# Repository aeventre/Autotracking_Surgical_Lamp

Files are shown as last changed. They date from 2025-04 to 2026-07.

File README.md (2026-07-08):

# AutoTracking Surgical Robot lamp



## Table of Contents
- [AutoTracking Surgical Robot lamp](#autotracking-surgical-robot-lamp)
  - [Table of Contents](#table-of-contents)
  - [Overview](#overview)
  - [Background](#background)
  - [Acknowledgments](#acknowledgments)
- [System Overview](#system-overview)
- [Software Design](#software-design)
  - [Setup](#setup)
  - [Package Overview](#package-overview)
    - [`command_manager`](#command_manager)
    - [`lamp_gui`](#lamp_gui)
    - [`remote_tracker`](#remote_tracker)
    - [`camera_calibration`](#camera_calibration)
    - [`goal_pose_executor`](#goal_pose_executor)
    - [`controller_coms`](#controller_coms)
    - [`surg_bot_description`](#surg_bot_description)
    - [`surg_bot_moveit_config`](#surg_bot_moveit_config)
  - [Launch Configurations](#launch-configurations)
- [Electrical Design](#electrical-design)
- [CAD](#cad)
  - [3D Printed Components of Surgical Robot](#3d-printed-components-of-surgical-robot)
  - [Sensors and Servos](#sensors-and-servos)
  - [Bill of materials for Surgical Robot](#bill-of-materials-for-surgical-robot)
  - [Bill of Materials for Surgical Robot Base](#bill-of-materials-for-surgical-robot-base)

## Overview
An open-source ROS 2 and MoveIt 2 surgical lamp capable of autonomous real-time tracking of a handheld remote using monocular vision and 3D pose estimation. 

## Background
This project aims to develop a solution to the challenges posed by modern surgical lamps,
particularly focused on the ceiling-mounted lamps. The proposed solution is a responsive
surgical lamp that uses real-time tracking and automated movement to adjust its lighting
position. This approach minimizes manual interaction, reduces delays and allows support staff
to remain focused on higher priority clinical responsibilities

# System Overview
  

# Software Design

This ROS 2 workspace contains all packages required for the Auto-Tracking Surgical Lamp system. The lamp uses 3D pose tracking of a handheld remote (via green ball detection) to plan and execute motions in real-time, with fallback modes for manual GUI control and demo sequences. The system is built using ROS 2 Jazzy and MoveIt 2.

## Setup

To build and source the workspace:

```bash
cd /path/to/ros2_ws
source /opt/ros/jazzy/setup.bash
rosdep install --from-paths src --ignore-src -r -y
colcon build
source install/setup.bash
```

## Package Overview

software_architecture

### `command_manager`

Manages the system's behavior based on user input. It switches between modes such as idle, manual control, tracking, zeroing, and demo.

**Subscriptions**
- `/system_mode` (`std_msgs/Int32`)
- `/remote_pose` (`geometry_msgs/PoseStamped`)
- `/remote_orientation` (`geometry_msgs/QuaternionStamped`)
- `/user_command` (`surg_lamp_msgs/UserCommand`)

**Publications**
- `/goal_pose` (`geometry_msgs/PoseStamped`)
- `/joint_commands` (`std_msgs/Float64MultiArray`)
- `/user_command` (`surg_lamp_msgs/UserCommand`)

---

### `lamp_gui`

PyQt5-based graphical user interface for interacting with the lamp.

**Features**
- Dropdown menu for system mode selection
- Sliders for manual joint control
- Buttons for triggering demo modes or resets
- Status label for system feedback

**Publications**
- `/system_mode` (`std_msgs/Int32`)
- `/joint_commands` (`std_msgs/Float64MultiArray`)
- `/user_command` (`surg_lamp_msgs/UserCommand`)

---

### `remote_tracker`

Tracks a green marker (ball) on a handheld remote using OpenCV and depth cameras. Estimates the 3D position and uses IMU orientation to compute the full pose.

**Inputs**
- RGB and depth images from stereo cameras
- Camera extrinsics from `camera_calibration`
- IMU orientation from the remote

**Outputs**
- `/remote_pose` (`geometry_msgs/PoseStamped`)
- `/remote_orientation` (`geometry_msgs/QuaternionStamped`)

---

### `camera_calibration`

Contains stereo camera calibration and extrinsic transform files.

**Contents**
- `camera_01.yaml`, `camera_02.yaml`: intrinsics for each camera
- `camera_01_to_base.yaml`, `camera_02_to_base.yaml`: transformations from camera to robot base frame

Used by the `remote_tracker` for accurate triangulation and transformation into the base frame.

---

### `goal_pose_executor`

Plans and executes motions from the current pose to the goal pose using MoveIt 2.

**Inputs**
- `/goal_pose` (`geometry_msgs/PoseStamped`)

**Behavior**
- Uses `MoveGroupInterface` to plan paths
- Sends joint angles to `/joint_commands`
- Reports failure if planning is unsuccessful

---

### `controller_coms`

Handles RS-485 serial communication with two microcontrollers that control the lamp's motors and lighting.

**Responsibilities**
- Sends joint angle commands to MCU1 and MCU2
- Receives and parses motor feedback
- Manages half-duplex communication (send then receive)
- Relays light mode and button state

**Serial Protocol**
- `mcu1`: `<joint1,joint2,joint3,joint4,lightmode>`
- `mcu2`: `<joint0>`
- Half-duplex format: send commands, then wait for and parse response

---

### `surg_bot_description`

URDF/Xacro model of the surgical lamp.

**Includes**
- Link and joint definitions
- Joint limits and axes
- Visual and collision meshes
- Base frame and end-effector frame definitions

Used for visualization and planning.

---

### `surg_bot_moveit_config`

MoveIt 2 configuration for the surgical lamp.

**Includes**
- Kinematics solvers
- OMPL planning pipeline
- SRDF and robot semantic info
- RViz and MoveGroup launch support

---

## Launch Configurations

```bash
# GUI
ros2 run lamp_gui lamp_gui

# Command manager
ros2 run command_manager command_manager

# Remote tracker
ros2 run remote_tracker remote_tracker_node

# Goal pose executor
ros2 run goal_pose_executor goal_pose_executor_node

# Controller communication
ros2 run controller_coms controller_coms_node
```

# Electrical Design

## Remote Design 


## PCB Design 


# Pictures




All links and joints links are avaiable to download in the CAD section as .STL and .SLDPRT

## 3D Printed Components of Surgical Robot
ABS was the material used to print the prototype. ABS and PETG would be good options to use as well

## Sensors and Servos 
Below is a list of sensors and motors being used 
- 160 KG Servos 
- 20 KG Servos
- Adafruit 9-DOF Orientation IMU Fusion Sensor
- Magnetic Encoder 
- NEMA 17
- Bluetooth/WiFi module
- Motor Drivers
- Orbbec 335 Cameras 

## Bill of materials for Surgical Robot
- Full HD webcam
- 4 channels IIC I2C logic level converter
- ESP32 Cam
- RS-485 MAX485 Transceiver
- 160 KG Servo
- Nema 17 Stepper
- Taidacent 12 wire 5A Slip Rings 
- USB to RS-485 Converter
- AS5600 Magnetic Encoder 
- Magnets 
- Laser Diodes
- LED Circle Array
- Raspberry Pi 5 8GB

## Bill of Materials for Surgical Robot Base

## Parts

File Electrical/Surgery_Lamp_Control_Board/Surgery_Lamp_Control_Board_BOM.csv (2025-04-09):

Reference | Qty | Value | Footprint | Digikey Part Number
R1,R2,R3,R4,R5,R6,R7,R8,R9,R10,R11,R12,R13,R16,R17 | 15 | 10k | Resistor_SMD:R_0805_2012Metric | YAG2132CT-ND
J1 | 1 | OSTVN05A150 | Alec_lib:CONN5_516x256_OST | ED10564-ND
Q1,Q2,Q3,Q4,Q5,Q6 | 6 | BSS138 | Package_TO_SOT_SMD:SOT-23-3 | BSS138-FDICT-ND
U2 | 1 | PCA9685PW | Package_SO:TSSOP-28_4.4x9.7mm_P0.65mm | 568-8366-5-ND
U1 | 1 | MAX485E | Package_SO:SOIC-8-1EP_3.9x4.9mm_P1.27mm_EP2.29x3mm | 4518-MAX485ESACT-ND
C1,C3 | 2 | 10uF | Capacitor_SMD:C_0805_2012Metric | 399-C0805C106K4PACTUCT-ND
C2,C4 | 2 | 0.1uF | Capacitor_SMD:C_0805_2012Metric | 399-C0805C104M5UACTUCT-ND
C5 | 1 | 47uF | Alec_lib:CAP_6.3 X 5.8_PAN | 399-18135-1-ND
MCU1 | 1 | RaspberryPi_Pico | Module:RaspberryPi_Pico_Common_Unspecified | 2648-SC0915CT-ND
R14,R15 | 2 | 20k | Resistor_SMD:R_0805_2012Metric | 13-RC0805FR-1020KLCT-ND
J8 | 1 | Stepper | Connector_PinSocket_2.54mm:PinSocket_1x04_P2.54mm_Vertical
J7 | 1 | joint4 | Connector_PinSocket_2.54mm:PinSocket_1x04_P2.54mm_Vertical
J6 | 1 | joint3 | Connector_PinSocket_2.54mm:PinSocket_1x04_P2.54mm_Vertical
J5 | 1 | joint2 | Connector_PinSocket_2.54mm:PinSocket_1x03_P2.54mm_Vertical
J4 | 1 | Joint 2 Encoder | Connector_PinSocket_2.54mm:PinSocket_1x05_P2.54mm_Vertical
J3 | 1 | Joint 1 Encoder | Connector_PinSocket_2.54mm:PinSocket_1x05_P2.54mm_Vertical
J2 | 1 | Headlamp | Connector_PinSocket_2.54mm:PinSocket_1x05_P2.54mm_Vertical
H1,H2,H3,H4 | 4 | MountingHole_Pad | MountingHole:MountingHole_3.2mm_M3_DIN965_Pad_TopBottom
A1 | 1 | Pololu_Breakout_DRV8825 | Module:Pololu_Breakout-16_15.2x20.3mm

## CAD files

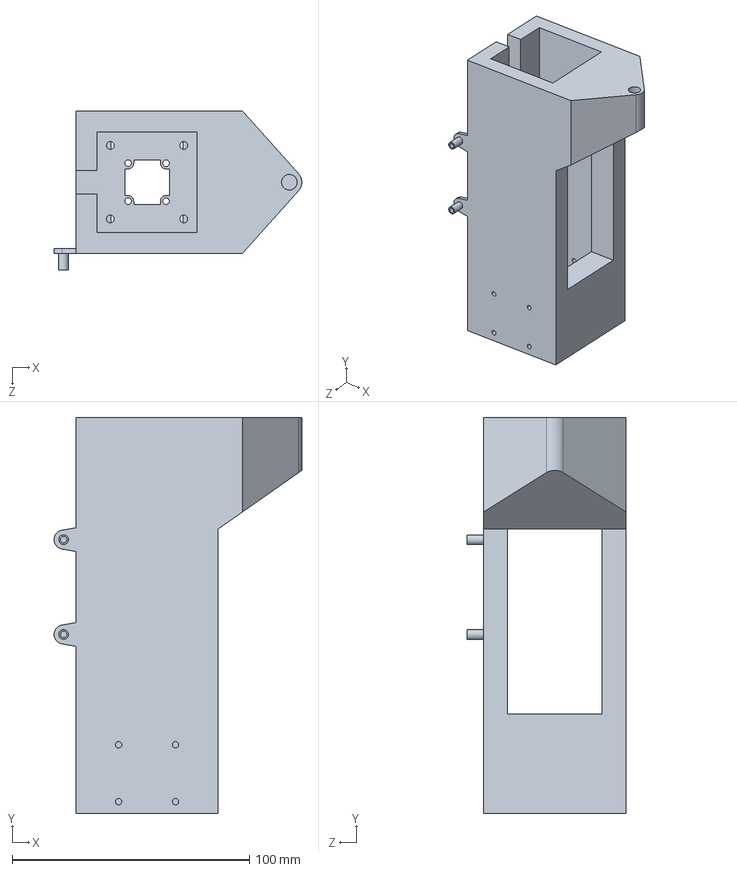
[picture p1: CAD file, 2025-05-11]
CAD/Lamp_Arm/Link2_V3.SLDPRT
104.5 x 167.0 x 67.0 mm

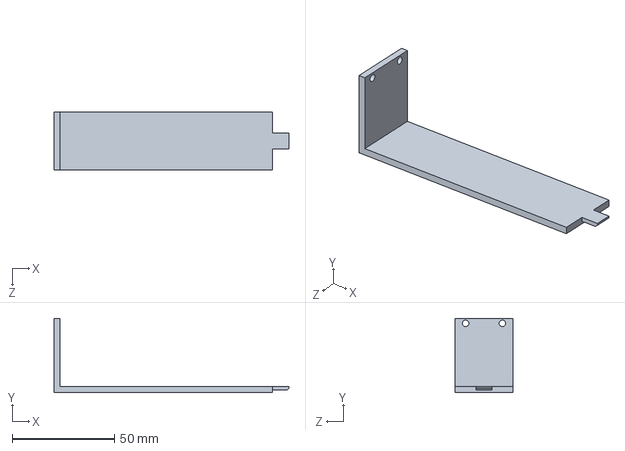
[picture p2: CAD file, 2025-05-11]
CAD/Remote/RemoteNEW_Back_V1.SLDPRT
115.0 x 36.2 x 28.2 mm

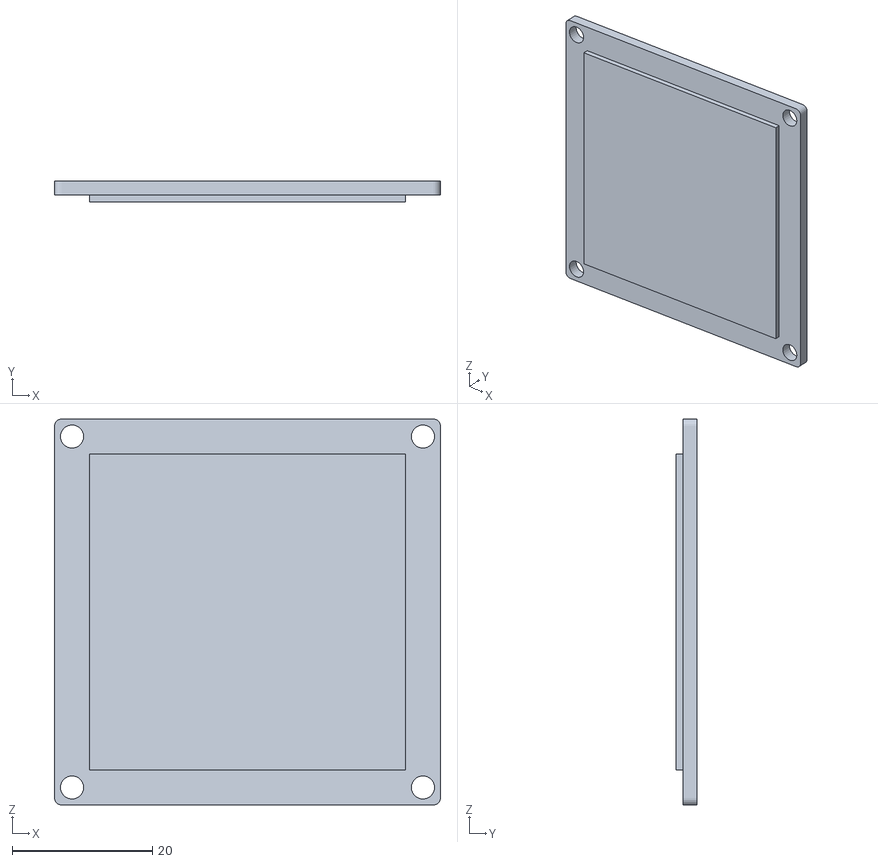
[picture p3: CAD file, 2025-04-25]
ros2_ws/src/surg_bot/surg_bot_description/meshes/AprilTag0_1.stl
55.0 x 3.00 x 55.0

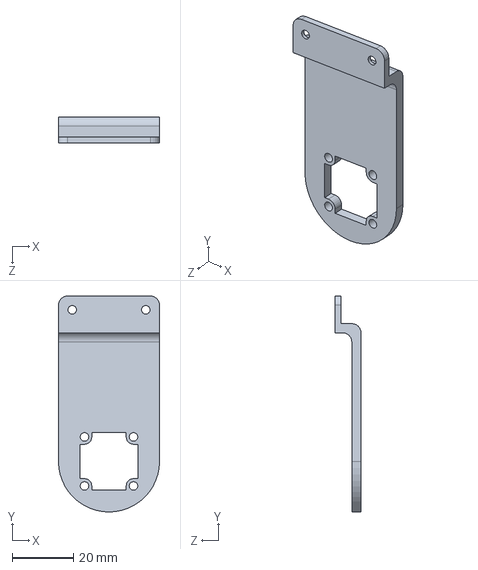
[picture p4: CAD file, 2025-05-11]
CAD/Lamp_Arm/EncoderMountV4.SLDPRT
33.0 x 70.5 x 8.50 mm

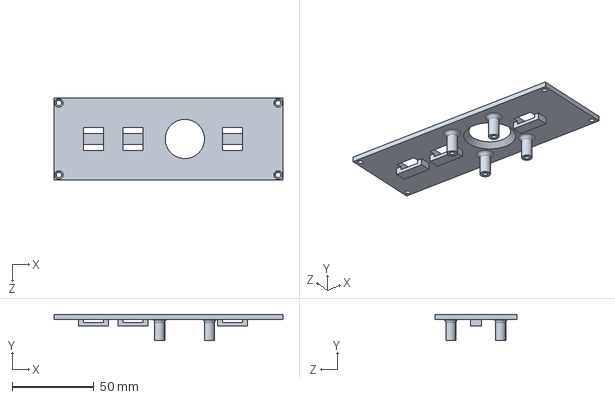
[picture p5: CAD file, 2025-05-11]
CAD/Remote/RemoteNEW_Cover_V1.SLDPRT
140.0 x 16.0 x 50.0 mm

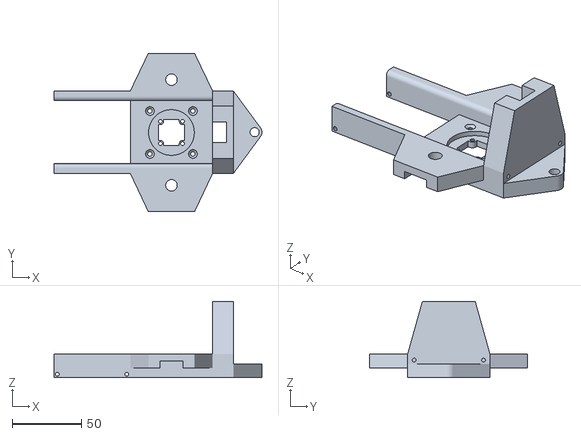
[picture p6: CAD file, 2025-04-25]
ros2_ws/src/surg_bot/surg_bot_description/meshes/base_connector_1.stl
150.0 x 114.3 x 55.1

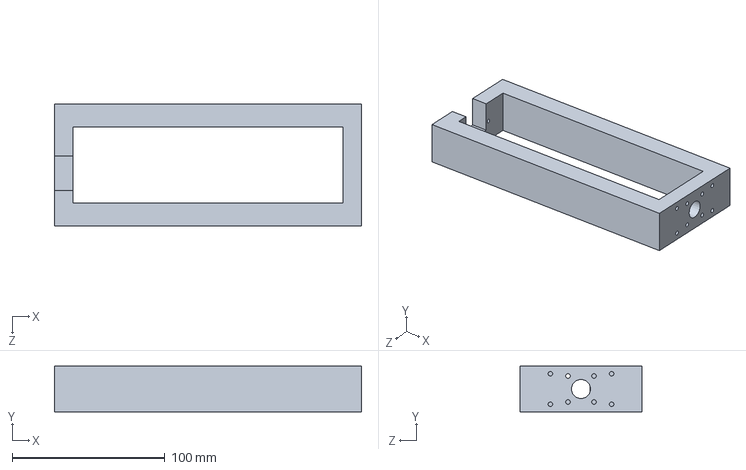
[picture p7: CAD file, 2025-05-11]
CAD/Lamp_Arm/Link3_V4.SLDPRT
201.2 x 30.0 x 80.0 mm

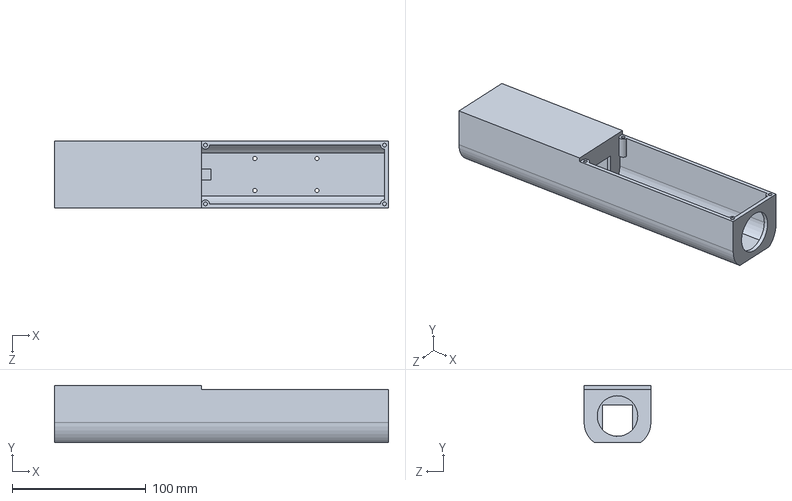
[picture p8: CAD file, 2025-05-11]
CAD/Remote/RemoteNEW_Body_V1.SLDPRT
250.0 x 43.0 x 50.0 mm

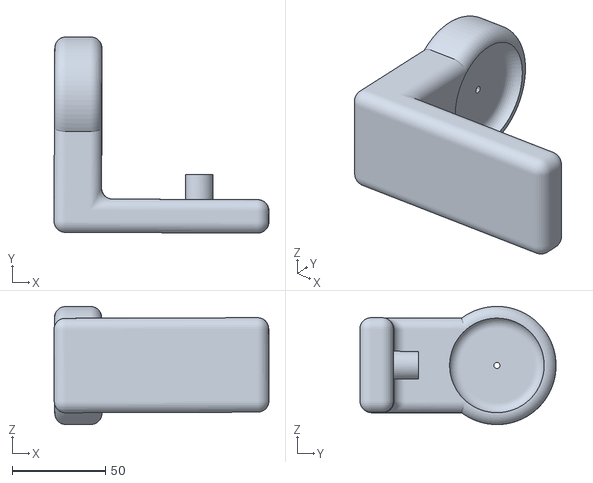
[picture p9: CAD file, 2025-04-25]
ros2_ws/src/surg_bot/surg_bot_description/meshes/link4_1.stl
115.6 x 105.5 x 63.5

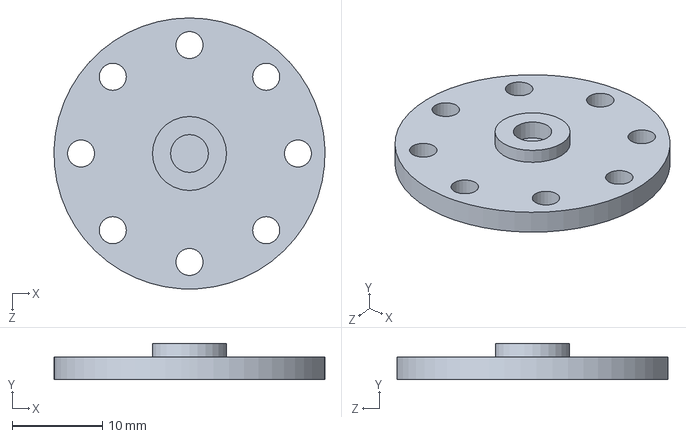
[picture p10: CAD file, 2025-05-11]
CAD/Lamp_Arm/MagnetMount_V2.SLDPRT
30.0 x 4.00 x 30.0 mm

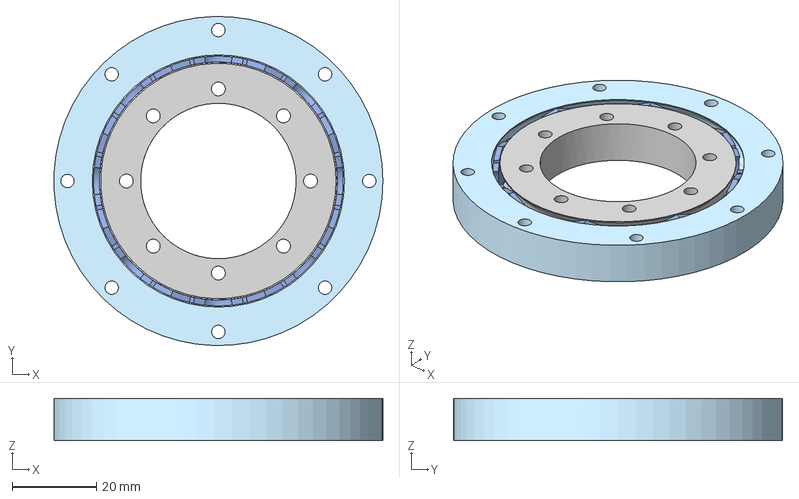
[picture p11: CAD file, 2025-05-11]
CAD/Lamp_Arm/DeepGrooveBearing.step
78.2 x 78.3 x 10.0 mm

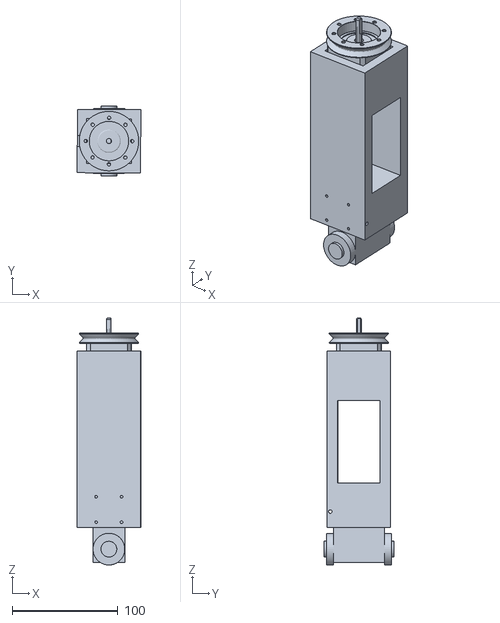
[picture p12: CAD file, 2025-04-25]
ros2_ws/src/surg_bot/surg_bot_description/meshes/link2_1_1.stl
60.2 x 66.5 x 233.5

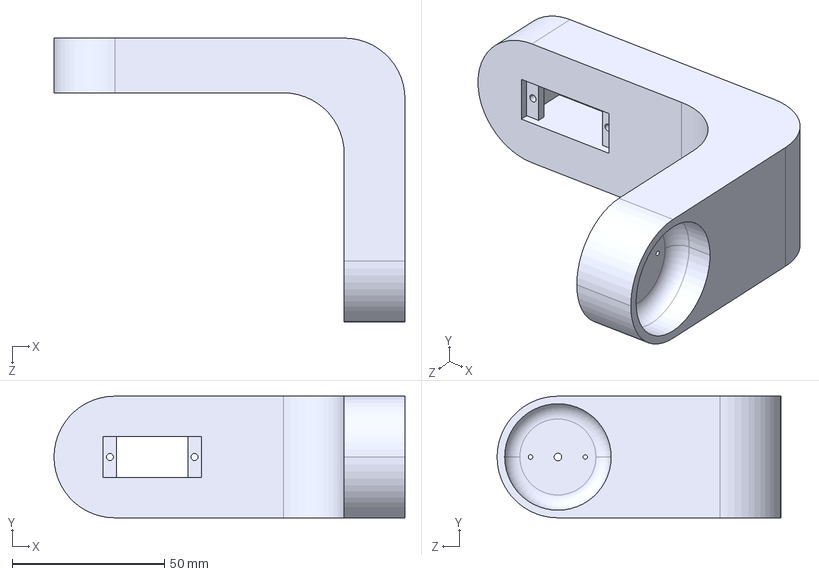
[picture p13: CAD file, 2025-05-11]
CAD/Lamp_Arm/Link4_V5.STEP
115.4 x 40.0 x 93.3 mm

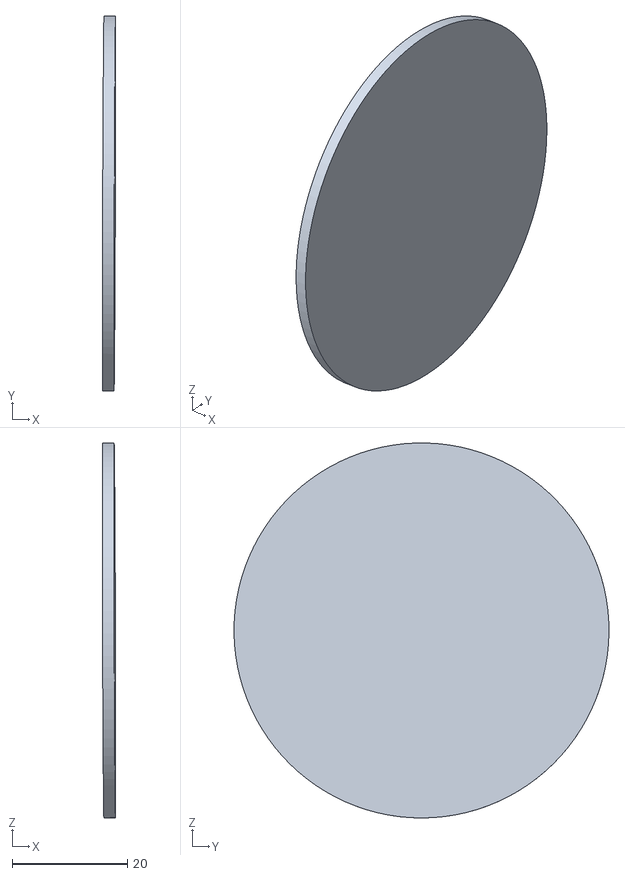
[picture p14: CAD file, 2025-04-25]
ros2_ws/src/surg_bot/surg_bot_description/meshes/end_effector_1.stl
2.33 x 65.0 x 65.0

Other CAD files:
ros2_ws/src/surg_bot/surg_bot_description/meshes/AprilTag1_1.stl
CAD/Lamp_Arm/Link1_P2.SLDPRT
ros2_ws/src/surg_bot/surg_bot_description/meshes/link3_1.stl
CAD/Lamp_Arm/HeadLamp_V4.SLDPRT
CAD/Lamp_Arm/EncoderMountV4.STL
CAD/Lamp_Arm/HeadLampCover.SLDPRT
CAD/Lamp_Arm/HeadLampCover.STL
CAD/Lamp_Arm/HeadLamp_V4.STL
CAD/Lamp_Arm/LampConnectorV12.SLDPRT
CAD/Lamp_Arm/LampConnectorV12.STL
CAD/Lamp_Arm/Link1_P1.SLDPRT
CAD/Lamp_Arm/Link1_P1.STL
CAD/Lamp_Arm/Link1_P2.STL
CAD/Lamp_Arm/Link2_V3.STL
CAD/Lamp_Arm/Link3_V4.STL
CAD/Lamp_Arm/Link4_V5.SLDPRT
CAD/Lamp_Arm/Link4_V5.STL
CAD/Lamp_Arm/MagnetMount_V2.STL
CAD/Remote/RemoteNEW_Back_V1.STL
CAD/Remote/RemoteNEW_Body_V1.STL
CAD/Remote/RemoteNEW_Cover_V1.STL
ros2_ws/src/surg_bot/surg_bot_description/meshes/base_link.stl
ros2_ws/src/surg_bot/surg_bot_description/meshes/fake_link_1.stl
ros2_ws/src/surg_bot/surg_bot_description/meshes/link1_1_1.stl
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

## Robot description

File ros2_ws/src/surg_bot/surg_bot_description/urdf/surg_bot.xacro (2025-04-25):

<?xml version="1.0" ?>
<robot name="surg_bot" xmlns:xacro="http://www.ros.org/wiki/xacro">

<xacro:include filename="$(find surg_bot_description)/urdf/materials.xacro" />
<xacro:include filename="$(find surg_bot_description)/urdf/surg_bot.trans" />
<xacro:include filename="$(find surg_bot_description)/urdf/surg_bot.gazebo" />
<link name="base_link">
  <inertial>
    <origin xyz="-4.031295976229773e-05 2.551630137478745e-06 -0.02955399218078996" rpy="0 0 0"/>
    <mass value="0.4069489619511855"/>
    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
  </inertial>
  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
</link>

<link name="link1_1_1">
  <inertial>
    <origin xyz="-0.16001007717101143 -1.5433885540422345e-05 -0.01760775000004948" rpy="0 0 0"/>
    <mass value="8.367890341080868"/>
    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
  </inertial>
  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
</link>

<link name="link2_1_1">
  <inertial>
    <origin xyz="0.000222277820202621 2.4740641813817415e-05 -0.11737411773568346" rpy="0 0 0"/>
    <mass value="3.3490679501648595"/>
    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
  </inertial>
  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
</link>

<link name="link3_1">
  <inertial>
    <origin xyz="0.1354592267935596 0.030192910648437193 0.00044866468104021173" rpy="0 0 0"/>
    <mass value="1.7602626049739658"/>
    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
  </inertial>
  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
</link>

<link name="link4_1">
  <inertial>
    <origin xyz="0.026057732789940877 -0.04507242698022944 8.680052417670003e-05" rpy="0 0 0"/>
    <mass value="1.4039319321687402"/>
    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
  </inertial>
  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
</link>

<link name="fake_link_1">
  <inertial>
    <origin xyz="-0.0025000443408709893 8.946959404469842e-06 -8.268459717741816e-06" rpy="0 0 0"/>
    <mass value="0.001098697673021953"/>
    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
  </inertial>
  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
</link>

<link name="AprilTag0_1"/>


<link name="base_connector_1">
  <inertial>
    <origin xyz="0.008739591761476772 -0.009261123091376765 0.013879262591046193" rpy="0 0 0"/>
    <mass value="0.8045670076781538"/>
    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
  </inertial>
  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
</link>

<link name="AprilTag1_1"/>

<link name="link5_1_1">
  <inertial>
    <origin xyz="-0.00044160365250938067 0.03911603505931648 3.168698741190523e-05" rpy="0 0 0"/>
    <mass value="0.38469776659589416"/>
    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
  </inertial>
  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
</link>

<link name="end_effector_1">
  <inertial>
    <origin xyz="0.0009999117915723155 -4.233375403692912e-06 3.279256363175609e-06" rpy="0 0 0"/>
    <mass value="0.05209742367356123"/>
    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
  </inertial>
  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
</link>

<joint name="joint0" type="revolute">
  <origin xyz="-1e-05 1e-05 -0.063784" rpy="0 0 0"/>
  <parent link="base_link"/>
  <child link="link1_1_1"/>
  <axis xyz="0.0 0.0 1.0"/>
  <limit upper="3.141593" lower="-3.141593" effort="100" velocity="100"/>
</joint>

<joint name="joint1" type="revolute">
  <origin xyz="-0.32002 0.0 -0.035216" rpy="0 0 0"/>
  <parent link="link1_1_1"/>
  <child link="link2_1_1"/>
  <axis xyz="0.0 0.0 1.0"/>
  <limit upper="3.141593" lower="-3.141593" effort="100" velocity="100"/>
</joint>

<joint name="joint2" type="revolute">
  <origin xyz="-0.000105 -0.03061 -0.204283" rpy="0 0 0"/>
  <parent link="link2_1_1"/>
  <child link="link3_1"/>
  <axis xyz="-0.003766 -0.999993 0.0"/>
  <limit upper="0.174533" lower="-1.570796" effort="100" velocity="100"/>
</joint>

<joint name="joint3" type="revolute">
  <origin xyz="0.254816 0.029741 0.000845" rpy="0 0 0"/>
  <parent link="link3_1"/>
  <child link="link4_1"/>
  <axis xyz="0.999987 -0.003766 0.003319"/>
  <limit upper="2.268928" lower="-2.268928" effort="100" velocity="100"/>
</joint>

<joint name="joint5" type="revolute">
  <origin xyz="0.014907 0.041545 4.9e-05" rpy="0 0 0"/>
  <parent link="link5_1_1"/>
  <child link="fake_link_1"/>
  <axis xyz="0.999987 -0.003766 0.003299"/>
  <limit upper="3.141593" lower="-3.141593" effort="100" velocity="100"/>
</joint>


<joint name="rigid1" type="fixed">
  <origin xyz="0.0 0.0094 -0.007" rpy="0 0 0"/>
  <parent link="base_link"/>
  <child link="base_connector_1"/>
</joint>

<joint name="tag0" type="fixed">
  <origin xyz="-0.0572 -0.041877 0.0275" rpy="1.5708 0 0"/>
  <parent link="base_connector_1"/>
  <child link="AprilTag0_1"/>
</joint>

<joint name="tag1" type="fixed">
  <origin xyz="-0.0572 0.023523 0.0275" rpy="-1.5708 -3.1416 0"/>
  <parent link="base_connector_1"/>
  <child link="AprilTag1_1"/>
</joint>

<joint name="joint4" type="revolute">
  <origin xyz="0.065091 -0.042116 0.000216" rpy="0 0 0"/>
  <parent link="link4_1"/>
  <child link="link5_1_1"/>
  <axis xyz="0.003766 0.999993 -0.0"/>
  <limit upper="2.268928" lower="-2.268928" effort="100" velocity="100"/>
</joint>

<joint name="slider" type="prismatic">
  <origin xyz="0.0 0.0 0.0" rpy="0 0 0"/>
  <parent link="fake_link_1"/>
  <child link="end_effector_1"/>
  <axis xyz="0.999987 -0.003766 0.003299"/>
  <limit upper="3.0" lower="0.0" effort="100" velocity="100"/>
</joint>

</robot>

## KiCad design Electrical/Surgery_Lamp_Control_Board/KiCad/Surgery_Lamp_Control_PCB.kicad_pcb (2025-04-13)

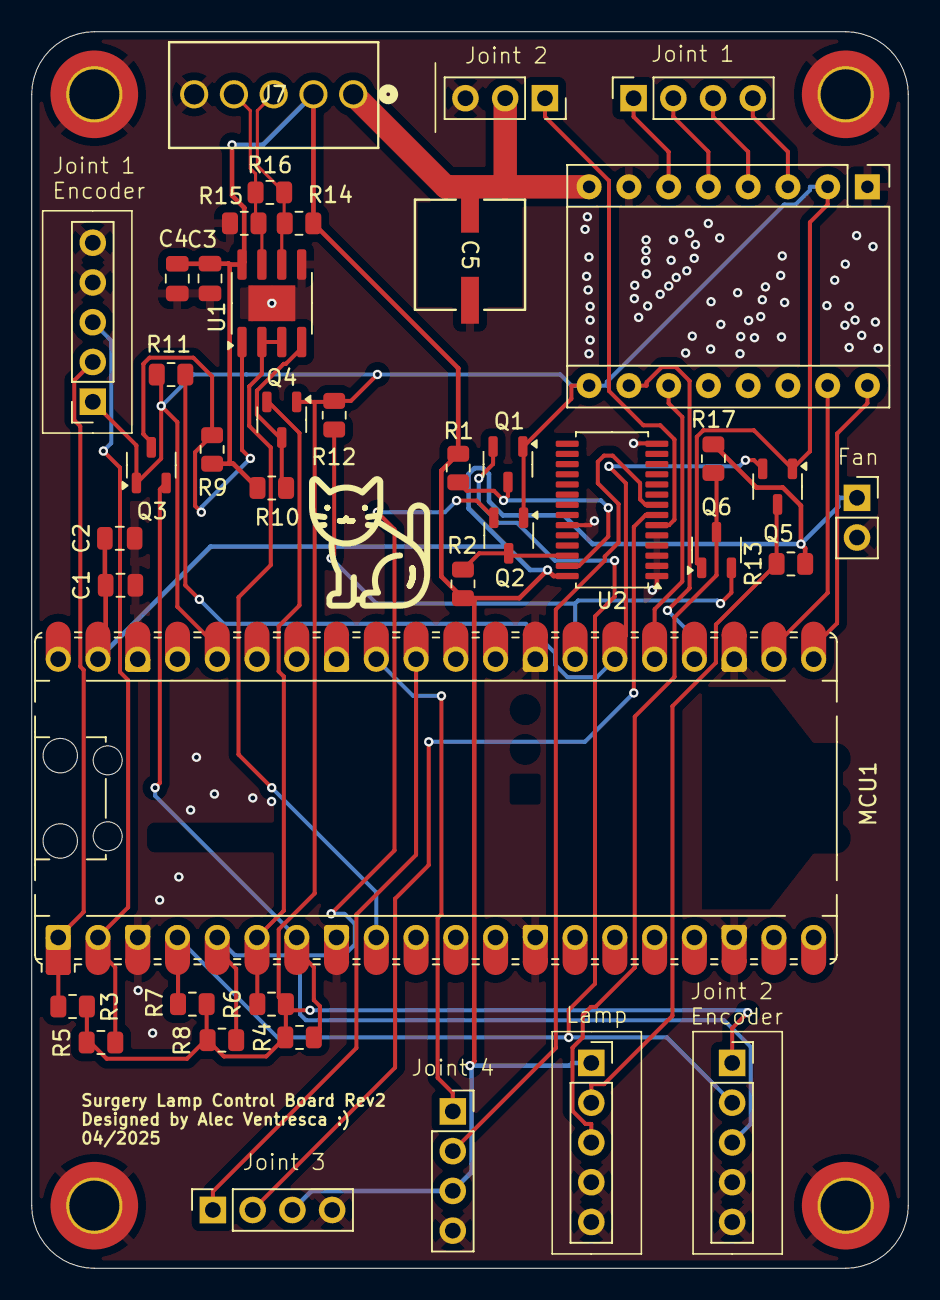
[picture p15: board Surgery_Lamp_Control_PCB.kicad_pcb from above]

Board: 2 copper layers, 56.0 x 79.0 mm, 45 parts (0 on the bottom side), 34 nets.

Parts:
A1: TMC2209 Stepper Driver; Pololu_Breakout-16_15.2x20.3mm
C1, C3: 10uF; C_0805_2012Metric
C2, C4: 0.1uF; C_0805_2012Metric
C5: 47uF; CAP_6.3 X 5.8_PAN
H1, H2, H3, H4: MountingHole_Pad; MountingHole_3.2mm_M3_DIN965_Pad_TopBottom
J1: joint2; PinSocket_1x03_P2.54mm_Vertical
J2: joint3; PinSocket_1x04_P2.54mm_Vertical
J3: joint4; PinSocket_1x04_P2.54mm_Vertical
J4: Headlamp; PinSocket_1x05_P2.54mm_Vertical
J5: Joint 1 Encoder; PinSocket_1x05_P2.54mm_Vertical
J6: Joint 2 Encoder; PinSocket_1x05_P2.54mm_Vertical
J7: OSTVN05A150; CONN5_516x256_OST
J8: Stepper; PinSocket_1x04_P2.54mm_Vertical
J9: Fan; PinSocket_1x02_P2.54mm_Vertical
MCU1: RaspberryPi_Pico; RaspberryPi_Pico_Common_Unspecified
Q1, Q2, Q3, Q4, Q5, Q6: BSS138; SOT-23-3
R1, R2, R3, R4, R5, R6, R7, R8, R9, R10, R11, R12, R13, R17: 10k; R_0805_2012Metric
R14, R15: 20k; R_0805_2012Metric
R16: 120; R_0805_2012Metric
U1: MAX485E; SOIC-8-1EP_3.9x4.9mm_P1.27mm_EP2.29x3mm
U2: PCA9685PW; TSSOP-28_4.4x9.7mm_P0.65mm

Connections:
3V3: A1.2 (VIO), A1.9 (EN), J5.1, J6.1, MCU1.36 (3V3), Q1.1 (G), Q2.1 (G), Q3.1 (G), Q4.1 (G), Q5.1 (G), Q6.1 (G), R3.1, R4.1, R5.1, R6.1, R7.1, R8.1, R11.1, R12.1
5V: C1.1, C2.1, C3.1, C4.1, J2.3, J3.3, J4.1, J7.2, J9.1, MCU1.39 (VSYS), R1.1, R2.1, R9.1, R10.1, R13.1, R14.1, R17.1, U1.8 (VCC), U2.28 (VDD)
24V: A1.8 (VMOT), C5.1, J1.2, J7.1
DIR: A1.16 (DIR), MCU1.21 (GPIO16)
GND: A1.1 (GND), A1.7 (GND), C1.2, C2.2, C3.2, C4.2, C5.2, H1.1, H2.1, H3.1, H4.1, J1.3, J2.4, J3.4, J4.4, J4.5, J5.4, J5.5, J6.4, J6.5, J7.5, J9.2, MCU1.3 (GND), MCU1.8 (GND), MCU1.13 (GND), MCU1.18 (GND), MCU1.23 (GND), MCU1.28 (GND), MCU1.38 (GND), R15.2, U1.5 (GND), U1.9, U2.1 (A0), U2.2 (A1), U2.3 (A2), U2.4 (A3), U2.5 (A4), U2.14 (VSS), U2.23 (*OE)
MS1: A1.10 (MS1), MCU1.24 (GPIO18)
MS2: A1.11 (MS2), MCU1.25 (GPIO19)
unnamed: A1.5 (1A), J8.2
unnamed: A1.6 (1B), J8.1
unnamed: A1.4 (2A), J8.3
unnamed: A1.3 (2B), J8.4
unnamed: J1.1, U2.6 (LED0)
unnamed: J2.2, U2.7 (LED1)
unnamed: J3.2, U2.8 (LED2)
unnamed: MCU1.26 (GPIO20), Q5.2 (S), R11.2
unnamed: MCU1.27 (GPIO21), Q6.2 (S), R12.2
unnamed: Q3.3 (D), R9.2, U1.1 (RO)
unnamed: Q4.3 (D), R10.2, U1.4 (DI)
RS+: J7.3, R14.2, R16.1, U1.6 (A)
RS-: J7.4, R15.1, R16.2, U1.7 (B)
RS_Enable: MCU1.9 (GPIO6), U1.2 (~RE), U1.3 (DE)
RX: MCU1.7 (GPIO5), Q3.2 (S), R4.2
SCL0: J5.3, MCU1.2 (GPIO1), R5.2
SCL1: J6.3, MCU1.5 (GPIO3), Q2.2 (S), R8.2
SCL1_5V: Q2.3 (D), R2.2, U2.26 (SCL)
SDA0: J5.2, MCU1.1 (GPIO0), R3.2
SDA1: J6.2, MCU1.4 (GPIO2), Q1.2 (S), R7.2
SDA1_5V: Q1.3 (D), R1.2, U2.27 (SDA)
STEP: A1.15 (STEP), MCU1.22 (GPIO17)
TX: MCU1.6 (GPIO4), Q4.2 (S), R6.2
joint3_Feedback: J2.1, MCU1.31 (GPIO26_ADC0)
joint4_Feedback: J3.1, MCU1.32 (GPIO27_ADC1)
laser_pointer: J4.3, Q6.3 (D), R17.2
neopixel: J4.2, Q5.3 (D), R13.2

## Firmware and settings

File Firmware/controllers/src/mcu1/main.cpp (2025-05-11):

#include <Arduino.h>
#include <Wire.h>
#include <Adafruit_PWMServoDriver.h>
#include <Adafruit_NeoPixel.h>

#include "ServoJoint.h"
#include "StepperJoint.h"
#include "EncoderLib.h"
#include "CommandParser.h"

// --- PCA9685 Driver ---
Adafruit_PWMServoDriver pca9685(0x40, Wire1);

// --- Servo Joints ---
ServoJoint joint2;
ServoJoint joint3;
ServoJoint joint4;

// --- Stepper + Encoder ---
StepperJoint stepperJoint;
EncoderLib stepperEncoder(Wire);

// --- RS‑485 Command Parser ---
CommandParser rs485;
CommandMessage cmdMsg;

// --- Joint 2 slew‑rate limiter globals ---
float joint2DesiredAngle   = 7.0f;
float joint2CommandedAngle = 7.0f;
const float joint2MaxDelta = 0.5f;

// --- Joint 2 & 3 & 4 offset globals ---
float joint2Offset = -5.0f;
float joint3Offset = 135.0f;
float joint4Offset = 113.0f;

// --- NeoPixel Ring & Laser ---
#define NEOPIXEL_PIN    20
#define NEOPIXEL_COUNT  24
#define LASER_PIN       21

Adafruit_NeoPixel ring(NEOPIXEL_COUNT, NEOPIXEL_PIN, NEO_GRB + NEO_KHZ800);

//------------------------------------------------------------------------------
// Apply the “INT” field: select a ring pattern *and* laser on/off
//------------------------------------------------------------------------------
void setLightMode(int mode) {
  switch (mode) {
    case 0:  // all off
      ring.clear();
      break;

    case 1:  // solid red
      for (int i = 0; i < NEOPIXEL_COUNT; i++)
        ring.setPixelColor(i, ring.Color(255, 0, 0));
      break;

    case 2:  // green chase
      {
        static uint8_t idx = 0;
        ring.clear();
        ring.setPixelColor(idx % NEOPIXEL_COUNT, ring.Color(0, 255, 0));
        idx++;
      }
      break;

    case 3:  // rainbow wipe
      for (int i = 0; i < NEOPIXEL_COUNT; i++) {
        uint16_t hue = map(i, 0, NEOPIXEL_COUNT - 1, 0, 65535);
        ring.setPixelColor(i, ring.gamma32(ring.ColorHSV(hue)));
      }
      break;

    default: // unknown → off
      ring.clear();
      break;
  }

  ring.show();

  // Laser = ON for any non-zero mode, OFF for mode==0
  digitalWrite(LASER_PIN, (mode != 0) ? HIGH : LOW);
}

//------------------------------------------------------------------------------
void setup()
{
  // --- USB‑Serial for debug ---
  Serial.begin(115200);
  delay(2000);

  // --- RS‑485 on Serial2 (Pico TX=4, RX=5) ---
  rs485.begin(Serial2);

  // --- Laser pin ---
  pinMode(LASER_PIN, OUTPUT);
  digitalWrite(LASER_PIN, LOW);

  // --- NeoPixel init ---
  ring.begin();
  ring.setBrightness(50);
  ring.clear();
  ring.show();

  // --- I2C and PCA9685 ---
  Wire1.setSDA(2);
  Wire1.setSCL(3);
  Wire1.begin();
  pca9685.begin();
  pca9685.setPWMFreq(50);
  delay(10);

  // --- Stepper Encoder (AS5600) ---
  stepperEncoder.begin(0, 1);
  delay(10);
  stepperEncoder.zero();
  Serial.println("Stepper encoder zeroed to current position.");

  // --- StepperJoint Setup ---
  stepperJoint.begin(17, 16, &stepperEncoder, 18, 19);
  stepperJoint.setMicrostepping(1);
  stepperJoint.setPIDGains(80.0f, 0.2f, 0.5f);
  stepperJoint.setTarget(stepperEncoder.getFilteredAngle());

  // --- Joint 2: Open Loop Servo ---
  joint2.attach(0, &pca9685, true);
  joint2.setFeedbackType(ServoJoint::NONE);
  joint2.setAngleRange(180.0f);
  joint2.setPulseRange(102, 512);
  joint2.setTargetAngle(joint2CommandedAngle);

  // --- Joint 3: Open Loop Servo w/ offset ---
  joint3.attach(1, &pca9685);
  joint3.setFeedbackType(ServoJoint::NONE);
  joint3.setAngleRange(270.0f);
  joint3.setPulseRange(102, 512);
  joint3.setTargetAngle(joint3Offset);

  // --- Joint 4: Open Loop Servo w/ offset ---
  joint4.attach(2, &pca9685);
  joint4.setFeedbackType(ServoJoint::NONE);
  joint4.setAngleRange(270.0f);
  joint4.setPulseRange(102, 512);
  joint4.setTargetAngle(joint4Offset);

  Serial.println("System initialized. Listening for RS‑485 commands.");
}

void loop()
{

  // --- Process incoming RS‑485 frame ---
  if (rs485.readCommand(cmdMsg))
  {
    // 1) stepper
    stepperJoint.setTarget(cmdMsg.a1);

    // 2) joint 2 (inverted)
    joint2DesiredAngle = -cmdMsg.a2;

    // 3) joints 3 & 4 with offsets
    joint3.setTargetAngle(cmdMsg.a3 + joint3Offset);
    joint4.setTargetAngle(cmdMsg.a4 + joint4Offset);

    // 4) lights + laser
    setLightMode(cmdMsg.lightMode);

    rs485.clearReceivedFlag();
    rs485.sendStatus(cmdMsg);
  }

  // --- Slew‑rate limit & apply Joint 2 ---
  {
    float diff = joint2DesiredAngle - joint2CommandedAngle;
    if (fabs(diff) > joint2MaxDelta)
      joint2CommandedAngle += joint2MaxDelta * (diff > 0 ? 1 : -1);
    else
      joint2CommandedAngle = joint2DesiredAngle;
    joint2.setTargetAngle(joint2CommandedAngle);
  }

  // --- Update all joints ---
  joint2.update();
  joint3.update();
  joint4.update();
  stepperJoint.update();
}

// No extra brace beyond this



    // --- Debug print to USB‑Serial ---
    // Serial.print("Stepper → ");
    // Serial.print(cmdMsg.a1, 1);
    // Serial.print(" | J2 → ");
    // Serial.print(cmdMsg.a2, 1);
    // Serial.print(" | J3 → ");
    // Serial.print(cmdMsg.a3, 1);
    // Serial.print(" | J4 → ");
    // Serial.println(cmdMsg.a4, 1);
//}

// #include "ServoJoint.h"
// #include <Adafruit_PWMServoDriver.h>
// #include <Arduino.h>
// #include <Wire.h>

// Adafruit_PWMServoDriver pca9685(0x40, Wire1);
// ServoJoint joint2;

// void setup()
// {
//     Serial.begin(115200);

//     Wire1.setSDA(2);
//     Wire1.setSCL(3);
//     Wire1.begin();

//     pca9685.begin();        // No args needed
//     pca9685.setPWMFreq(50); // 50Hz for servos

//     joint2.attach(0, &pca9685); // pass pointer here because ServoJoint expects it
//     joint2.setFeedbackType(ServoJoint::NONE);

//     Serial.println("ServoJoint Open Loop Test Ready");
// }

// void loop()
// {
// joint2.setTargetAngle(0);
// joint2.update();
// delay(1000);

// joint2.setTargetAngle(90);
// joint2.update();
// delay(1000);

// joint2.setTargetAngle(180);
// joint2.update();
// delay(1000);

//     pca9685.setPWM(0, 0, 150);
//     delay(1000); // 0 degrees
//     pca9685.setPWM(0, 0, 375);
//     delay(1000); // 90 degrees
//     pca9685.setPWM(0, 0, 600);
//     delay(1000); // 180 degrees
// }

// #include "CommandParser.h"
// #include "EncoderLib.h"
// #include "StepperJoint.h"
// #include "ServoJoint.h"
// #include <Adafruit_NeoPixel.h>
// #include <Adafruit_PWMServoDriver.h>
// #include <Arduino.h>

// // --- Objects ---
// StepperJoint joint1;
// EncoderLib encoder1(Wire);
// ServoJoint servo1, servo2, servo3;
// Adafruit_PWMServoDriver pwm = Adafruit_PWMServoDriver();
// CommandParser parser;
// CommandMessage desired;
// CommandMessage current;

// void handleLightMode(int mode);
// void laserOn();
// void laserOff();
// void laserBlink();
// void pixelsOff();
// void pixelsWhite();
// void pixelLightShow();
// void rainbowCycle(uint8_t wait);

// // --- Constants ---
// static constexpr uint8_t dirPin1 = 16;
// static constexpr uint8_t stepPin1 = 17;
// static constexpr uint8_t laserPin = 21;
// static constexpr uint8_t ledPin = 20; // NeoPixel ring
// static constexpr uint8_t builtInLED = 25;

// // --- NeoPixel setup ---
// #define LED_COUNT 24
// #define BRIGHTNESS 255
// Adafruit_NeoPixel strip(LED_COUNT, ledPin, NEO_GRBW + NEO_KHZ800);

// // --- Variables ---
// uint8_t lightMode = 0;

// void setup()
// {
//     Serial.begin(115200);
//     parser.begin(Serial2); // Sets pins for Serial2 so other libs don't need to

//     // Initialize PCA9685 for servos
//     pwm.begin();
//     pwm.setPWMFreq(50); // 50 Hz for servos

//     // Initialize encoder and stepper
//     encoder1.begin(0, 1); // SDA = GPIO 0, SCL = GPIO 1
//     joint1.begin(stepPin1, dirPin1, &encoder1);
//     joint1.calibrateFromEncoder();
//     joint1.setPIDGains(5, 1, 0.5);

//     // Attach servos
//     servo1.attach(0, &pwm);
//     servo2.attach(1, &pwm);
//     servo3.attach(2, &pwm);

//     // Setup NeoPixel strip
//     strip.begin();
//     strip.setBrightness(BRIGHTNESS);
//     strip.show(); // Start with all pixels off

//     // Setup laser pin
//     pinMode(laserPin, OUTPUT);
//     digitalWrite(laserPin, LOW);

//     // Built-in LED always ON
//     pinMode(builtInLED, OUTPUT);
//     digitalWrite(builtInLED, HIGH);
// }

// void loop()
// {
//     parser.readCommand(desired);
//     joint1.update();
//     servo1.update();
//     servo2.update();
//     servo3.update();

//     if (parser.messageReceived())
//     {
//         joint1.setTarget(desired.a1);
//         servo1.setTargetAngle(desired.a2);
//         servo2.setTargetAngle(desired.a3);
//         servo3.setTargetAngle(desired.a4);

//         current.lightMode = desired.lightMode;
//         current.a1 = joint1.getCurrentAngle();
//         current.a2 = servo1.getCurrentAngle();
//         current.a3 = servo2.getCurrentAngle();
//         current.a4 = servo3.getCurrentAngle();

//         parser.sendStatus(current);
//         parser.clearReceivedFlag();

//         lightMode = desired.lightMode;
//     }

//     // Handle lights and laser modes
//     switch (lightMode)
//     {
//         case 1: // All OFF
//             digitalWrite(laserPin, LOW);
//             strip.clear();
//             strip.show();
//             break;

//         case 2: // Laser ON only
//             digitalWrite(laserPin, HIGH);
//             strip.clear();
//             strip.show();
//             break;

//         case 3: // White LEDs ON only
//             digitalWrite(laserPin, LOW);
//             strip.fill(strip.Color(0, 0, 0, 255)); // Pure white
//             strip.show();
//             break;

//         case 4: // Laser + White LEDs
//             digitalWrite(laserPin, HIGH);
//             strip.fill(strip.Color(0, 0, 0, 255));
//             strip.show();
//             break;

//         case 5: // Laser blinking + NeoPixel light show
//             static uint32_t lastToggle = 0;
//             if (millis() - lastToggle > 500)
//             {
//                 digitalWrite(laserPin, !digitalRead(laserPin)); // Toggle laser
//                 lastToggle = millis();
//             }
//             rainbowCycle(5);
//             break;

//         default:
//             break;
//     }
// }

// // --- Rainbow animation for case 5 ---
// void rainbowCycle(uint8_t wait)
// {
//     static uint16_t j = 0;
//     j++;

//     for (uint16_t i = 0; i < strip.numPixels(); i++)
//     {
//         strip.setPixelColor(i, strip.gamma32(strip.ColorHSV((i * 65536L / strip.numPixels() + j*10) & 0xFFFF)));
//     }
//     strip.show();
//     delay(wait);
// }
    joint2.update();
    joint3.update();
    joint4.update();
    stepperJoint.update();

    if (parser.readCommand(cmd))
    {
        joint2.setTargetAngle(cmd.a1);
        joint3.setTargetAngle(cmd.a2);
        joint4.setTargetAngle(cmd.a3);
        stepperJoint.setTarget(cmd.a4);
    }

  }
  
// ====================================================================
// Test code for ServoJoint
// =========================


    CommandMessage status;
    status.a1 = joint2.getTargetAngle();
    status.a2 = joint3.getCurrentAngle();
    status.a3 = joint4.getCurrentAngle();
    status.a4 = stepperJoint.getCurrentAngle();
    status.lightMode = cmd.lightMode;
    parser.sendStatus(status);


    delay(20);
}

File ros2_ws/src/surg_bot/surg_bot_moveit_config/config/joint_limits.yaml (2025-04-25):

# joint_limits.yaml allows the dynamics properties specified in the URDF to be overwritten or augmented as needed

# For beginners, we downscale velocity and acceleration limits.
# You can always specify higher scaling factors (<= 1.2.0) in your motion requests.  # Increase the values below to 1.2.0 to always move at maximum speed.
default_velocity_scaling_factor: 0.1
default_acceleration_scaling_factor: 0.1

# Specific joint properties can be changed with the keys [max_position, min_position, max_velocity, max_acceleration]
# Joint limits can be turned off with [has_velocity_limits, has_acceleration_limits]
joint_limits:
  joint0:
    has_velocity_limits: true
    max_velocity: 2.0
    has_acceleration_limits: true
    max_acceleration: 2.0
  joint1:
    has_velocity_limits: true
    max_velocity: 2.0
    has_acceleration_limits: true
    max_acceleration: 2.0
  joint2:
    has_velocity_limits: true
    max_velocity: 2.0
    has_acceleration_limits: true
    max_acceleration: 2.0
  joint3:
    has_velocity_limits: true
    max_velocity: 2.0
    has_acceleration_limits: true
    max_acceleration: 2.0
  joint4:
    has_velocity_limits: true
    max_velocity: 2.0
    has_acceleration_limits: true
    max_acceleration: 2.0
  joint5:
    has_velocity_limits: true
    max_velocity: 2.0
    has_acceleration_limits: true
    max_acceleration: 2.0
  slider:
    has_velocity_limits: true
    max_velocity: 2.0
    has_acceleration_limits: true
    max_acceleration: 2.0

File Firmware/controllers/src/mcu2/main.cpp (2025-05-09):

// main.ino

#include "EncoderLib.h"
#include "StepperJoint.h"
#include <Arduino.h>

float readJoint0Command();
void readPIDCommand();

#define stepPin 3
#define dirPin  2

StepperJoint joint0;
EncoderLib   encoder(Wire);

void setup() {
    // Motor pins
    pinMode(dirPin,  OUTPUT);
    pinMode(stepPin, OUTPUT);
    pinMode(4,       OUTPUT);
    pinMode(5,       OUTPUT);

    Serial.begin(115200);

    // Encoder init & zero at startup
    encoder.begin(A4, A5);
    encoder.zero();

    // Joint init & zero calibration
    joint0.begin(stepPin, dirPin, &encoder, 4, 5);
    joint0.calibrateFromEncoder();

    // Initial PID & target
    joint0.setPIDGains(5.5f, 2.0f, 0.5f);
    joint0.setDeadband(0.5f);    // <–– within ±0.5° no ticking
    joint0.setTarget(0.0f);

}

void loop() {
    // Angle‐target commands: <<angle>>
    float newTarget = readJoint0Command();
    if (!isnan(newTarget)) {
        joint0.setTarget(newTarget);
        Serial.print("New target: ");
        Serial.println(newTarget);
    }

    // PID tuning commands: <P<value>>, <I<value>>, <D<value>>
    readPIDCommand();

    // Run control loop
    joint0.update();
}

void readPIDCommand() {
    static String input;
    static bool   receiving = false;

    while (Serial.available()) {
        char c = Serial.read();

        if (c == '<') {
            input     = "";
            receiving = true;
        }
        else if (c == '>' && receiving) {
            receiving = false;
            float val = input.substring(1).toFloat();

            if (input.startsWith("P")) {
                joint0.setKp(val);
                Serial.print("Kp = ");
                Serial.println(val);
            }
            else if (input.startsWith("I")) {
                joint0.setKi(val);
                Serial.print("Ki = ");
                Serial.println(val);
            }
            else if (input.startsWith("D")) {
                joint0.setKd(val);
                Serial.print("Kd = ");
                Serial.println(val);
            }
        }
        else if (receiving) {
            input += c;
        }
    }
}

float readJoint0Command() {
    static String input;
    static bool   receiving = false;

    while (Serial.available()) {
        char c = Serial.read();

        if (c == '<') {
            input     = "";
            receiving = true;
        }
        else if (c == '>' && receiving) {
            receiving = false;
            return input.toFloat();
        }
        else if (receiving) {
            input += c;
        }
    }
    return NAN;
}

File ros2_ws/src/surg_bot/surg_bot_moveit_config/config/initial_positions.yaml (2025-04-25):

# Default initial positions for surg_bot's ros2_control fake system

initial_positions:
  joint0: 0
  joint1: 0
  joint2: 0
  joint3: 0
  joint4: 0
  joint5: 0
  slider: 0.1

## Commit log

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2024-10-07 Added URDF file for modeling the robot arm
    [Base.STL, Link1.STL, Link2.STL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]
2024-10-07 urdf file geometries are now correct and functional, still can't load stl's into rviz
    [Base.stl, Link1.stl, Link2.stl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]
2024-10-14 Properly registered ROS2 packages
    [surg_bot_description.urdf]
2024-10-25 Deleted Even more unnecessary files
    [Base.STL, Base.stl, Link1.STL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]
2024-10-25 Moving stuff around
    [Base.STL, Link1.STL, Link2.STL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]
2024-10-31 Added python package for the hand tracking algorithm
    [surg_bot_description.csv, surg_bot_description.urdf]
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2025-02-26 Add surg_bot_description package with URDF models and configuration files
    [Base.STL, Link1.STL, Link2.STL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]
2025-02-27 Add surg_bot_description package with URDF models and configuration files; remove obsolete files
    [Base.STL, Link1.STL, Link2.STL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]
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2025-02-27 Update package.xml and setup.cfg to reflect package name change to kinematics_2d; remove obsolete files and enhance test initialization.
2025-02-27 Update serial_coms_node to use Float64MultiArray for joint_angles and improve serial data formatting
2025-02-27 Add initial implementation of serial_coms package for sending joint angles to microcontroller
2025-03-10 Create Wiring Schematic for Arm
    [schematic.kicad_pcb, schematic.kicad_sch]
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2025-03-20 Rev 1 of electrical schematic
    [schematic.kicad_sch]
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2025-03-22 Update platformio configuration to refine build source filters for mcu1 and mcu2
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2025-03-23 Refactor AS5600Interpolator class: streamline initialization, improve angle reading, and enhance motor control logic
2025-03-23 Refactor encoderLib: replace AS5600Interpolator with EncoderLib, enhancing angle reading and motor control logic
2025-03-23 Refactor EncoderLib: separate calibration logic into calibrateWithStepper method and improve code readability
2025-03-25 Update platformio configuration and implement main logic for mcu2 with servo control and command reception
2025-03-25 Update main logic in mcu2 to send current joint positions to ROS
2025-03-25 Update platform configuration for mcu2 to use Atmel AVR and Arduino framework
2025-03-25 Implement AS5600 encoder integration: add setup and loop functions for reading position and connection status
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2025-03-27 Refactor main.cpp: replace AS5600 sensor with EncoderLib for improved angle reading and initialization
    [main.cpp]
2025-03-27 Replace AS5600 encoder with EncoderLib: update setup and loop functions for improved angle readings
    [main.cpp]
2025-04-02 Complete Rev1 of Control Board PCB
    [A4988.kicad_sch, MAX485.kicad_sch, PCA9685.kicad_sch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]
2025-04-02 Remove obsolete files and add .gitignore for Surgery Lamp Control Board
    [A4988.kicad_sch, MAX485.kicad_sch, PCA9685.kicad_sch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]
2025-04-02 Add .gitignore for Surgery Lamp Control Board and remove obsolete files
    [A4988.kicad_sch, MAX485.kicad_sch, PCA9685.kicad_sch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]
2025-04-03 Update .gitignore to exclude PlatformIO files and add new .gitignore for Surgery Lamp Control Board
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2025-04-03 Update hand position publisher to improve hand detection and replace camera index; add launch file and remove outdated tests
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2025-04-06 Refactor mcu1 firmware to use DRV8834 driver and update library dependencies; add error check for text_on_edge_cuts in PCB design
    [main.cpp]
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2025-04-09 Replace surg_bot_description with updated CAD model
    [Base.STL, Link1.STL, Link2.STL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]
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2025-04-10 Update platform configuration for mcu2 and clean up KiCad files; remove unused autosave and lock files
    [Surgery_Lamp_Control_PCB.kicad_sch]
2025-04-13 Update Surgery Lamp Control PCB files
    [Surgery_Lamp_Control_PCB.kicad_pcb]
2025-04-13 Remove lamp_1 mesh and update URDF references to link5_1 and end_effector_1
    [end_effector_1.stl, link5_1.stl, surg_bot.xacro]
2025-04-13 Add initial configuration files for surg_bot_moveit_config package
    [joint_limits.yaml, surg_bot.ros2_control.xacro, surg_bot.urdf.xacro]
2025-04-13 Remove obsolete mesh files and update URDF references for improved model accuracy
    [base_link.stl, end_effector_1.stl, end_effector_1_1.stl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]
2025-04-13 Change description to fix base origin
    [base_link.stl, end_effector_1_1.stl, link1_1_1.stl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]
2025-04-13 Fixed all description and config files
    [surg_bot.xacro]
2025-04-15 Add goal pose calculator node and launch configuration
    [Surgery_Lamp_Control_PCB.step]
2025-04-15 Update joint limits and configuration for goal pose executor; add sensor configuration
    [joint_limits.yaml]
2025-04-16 Update joint velocity limits in configuration for improved safety
    [joint_limits.yaml]
2025-04-16 Refactor joint names to lowercase and update related configurations for consistency
    [joint_limits.yaml, ros2_controllers.yaml, surg_bot.ros2_control.xacro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]
2025-04-17 Fix URDF for shorter link3
    [end_effector_1_1.stl, joint_limits.yaml, link1_1_1.stl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]
2025-04-17 Got all the IK working, just need to do the execution
    [end_effector_1_1.stl, joint_limits.yaml, link4_1.stl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]
2025-04-17 Refactor communication node to use Float64MultiArray for joint commands and add user command subscription; improve error handling for insufficient joint command values.
    [coms_node.py]
2025-04-18 Remove outdated copyright and linter test files; add new launch files for controller management and warehouse database integration.
    [ros2_controllers.yaml]
2025-04-18 Organized packages into folders
    [base_link.stl, end_effector_1_1.stl, joint_limits.yaml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]
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2025-04-24 Update URDF to include apriltags
    [base_connector_1.stl, end_effector_1_1.stl, link1_1_1.stl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]
2025-04-25 Got the offset working with the IK
    [AprilTag0_1.stl, AprilTag1_1.stl, base_connector_1.stl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]
2025-04-25 Fix coordinates of April Tags on URDF
    [surg_bot.xacro]
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2025-04-26 Add launch files for spawning controllers and warehouse database
    - Created `spawn_controllers.launch.py` to facilitate the spawning of controllers for the `surg_bot` MoveIt configuration.
    - Created `warehouse_db.launch.py` to set up the warehouse database for the `surg_bot` MoveIt configuration.
    - Both launch files utilize the `MoveItConfigsBuilder` for configuration management.
    [AprilTag0_1.stl, AprilTag1_1.stl, base_connector_1.stl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]
2025-04-26 Switched to Arcu markers for calibration, fixed crashing bugs, only need to verify accuracy
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2025-04-29 Enhance ServoJoint functionality: add reversed attachment option, streamline angle setting, and update main application logic for joint2
    [main.cpp]
2025-04-30 Add autosave lock file for Surgery Lamp Control PCB
    [Surgery_Lamp_Control_PCB.kicad_sch]
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2025-05-01 Added two missing pins to mcu 2 code in mcu 1 branch
    [main.cpp]
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2025-05-04 RS-485 fix to send a recieve message when sent data
    [main.cpp]
2025-05-04 Added wrist tracker package. Working out bugs in remote tracker. Fixed bugs in command manager
    [coms_node.py]
2025-05-04 Fixed camera numbering and syncing issues due to confusing orbecc docs
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2025-05-09 Add final prototype CAD for remote and arm
    [DeepGrooveBearing.step, EncoderMountV4.SLDPRT, EncoderMountV4.STL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]
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
